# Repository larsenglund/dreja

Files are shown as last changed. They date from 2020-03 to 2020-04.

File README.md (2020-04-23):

# Dreja
DIY potter's wheel build from a broken hoverboard.

# Hardware
One of the wheel motors from the hoverboard/balance board is user as motor in the potter's wheel. The motor is controlled from a ESP32 via a brushless motor speed controller.

## Bill of materials
The hardware consists of
* Hoverboard, $0-? (I got mine for $30)
* Brushless Motor Speed Controller BLDC Driver Board with Hall (15A 500W DC12V-36V), $12
* ESP32 Development Board, $9
* Power supply (DC36V 10A 360W AC85-265V), $23
* Potentiometer for pedal (I used a 50k PTV09A-4025F-B503), $1
* Large bucket
* MDF + Scrap wood

Total cost: $60 (assuming you have the last two items on the list)

## Whishlist
Use the existing controlboard from the hoverboard to control the motor. There is a project that has done this for a different PCB than the one in my hoverboard, maybe it could easily be adapted.

## Assembly
First the motor is extracted from the hoverboard

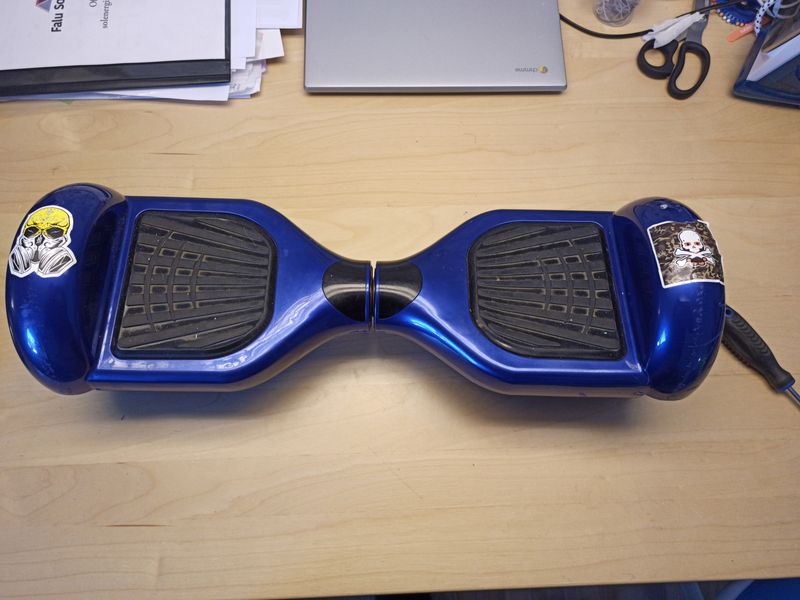
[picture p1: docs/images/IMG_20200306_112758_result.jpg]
Hoverboard1

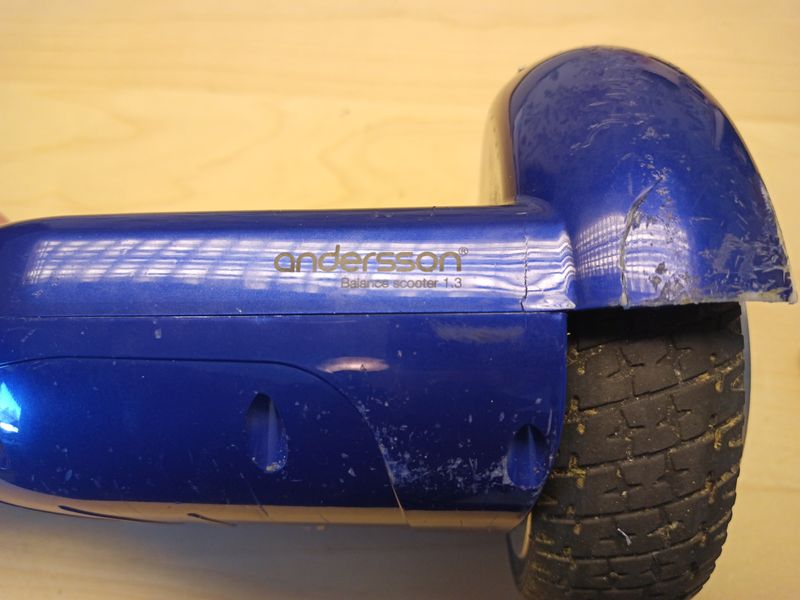
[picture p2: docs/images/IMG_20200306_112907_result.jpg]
Hoverboard2

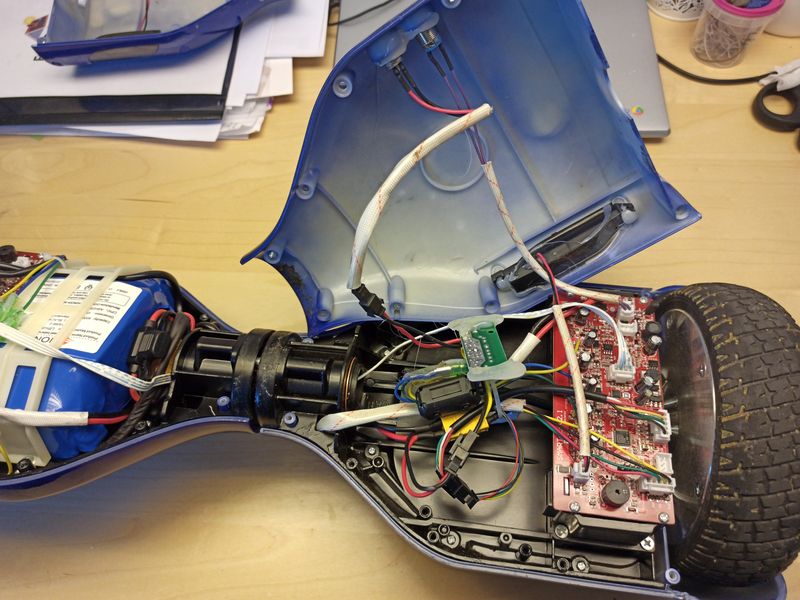
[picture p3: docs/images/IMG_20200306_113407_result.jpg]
Hoverboard3

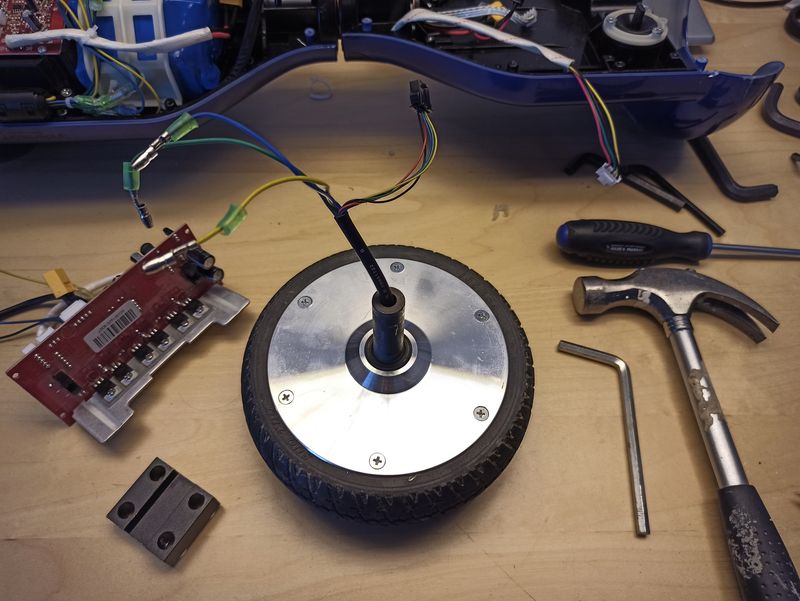
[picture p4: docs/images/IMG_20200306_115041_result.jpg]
Hoverboard4


### QS-909 JYQD
Low cost brushless motor driver with direction and speed control
12~36V, 500W (with heat sink) (http://grauonline.de/wordpress/?page_id=3122)

Pin description
* 5v       5v output
* EL       Motor enable input (5v)
* Signal   speedometer output
* Z/F      forward/reverse control (5v/GND)
* VR       speed control (0..5v)
* GND      ground

# Software
Software for the ESP32 is created with PlatformIO and allow speed control via a foot pedal. The ESP also serves up a captive portal that's used for remote monitoring and control.

Pin selection was made using this information.

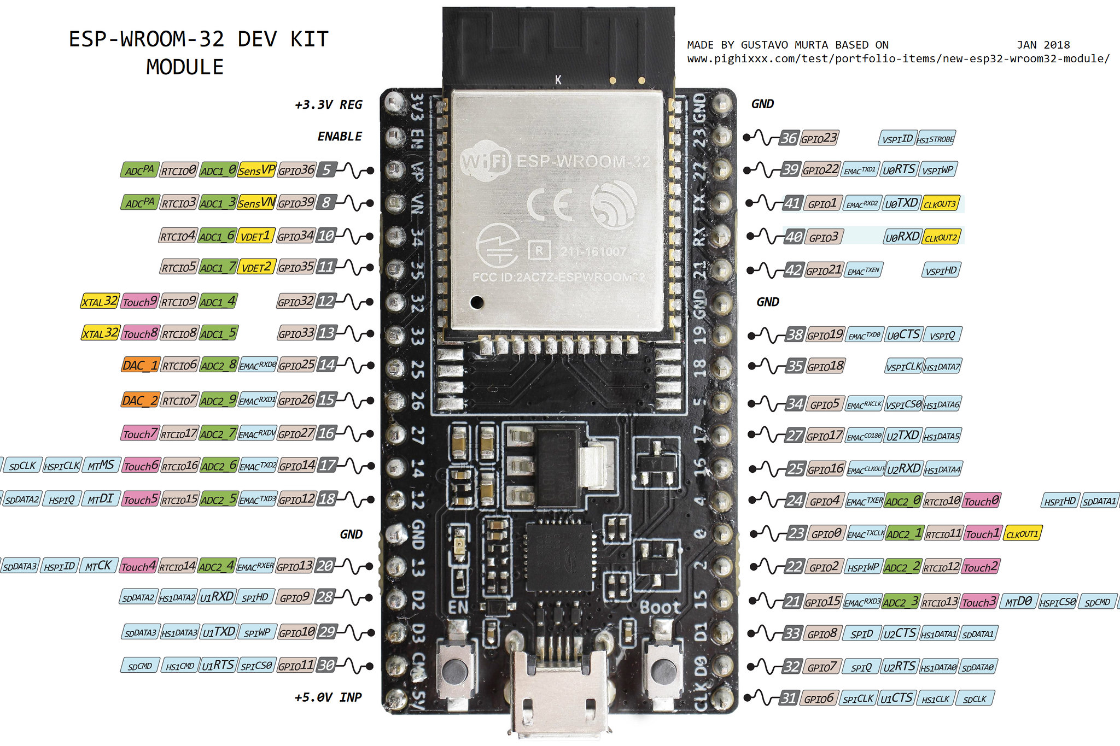
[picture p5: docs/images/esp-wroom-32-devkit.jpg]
ESP dev kit pins


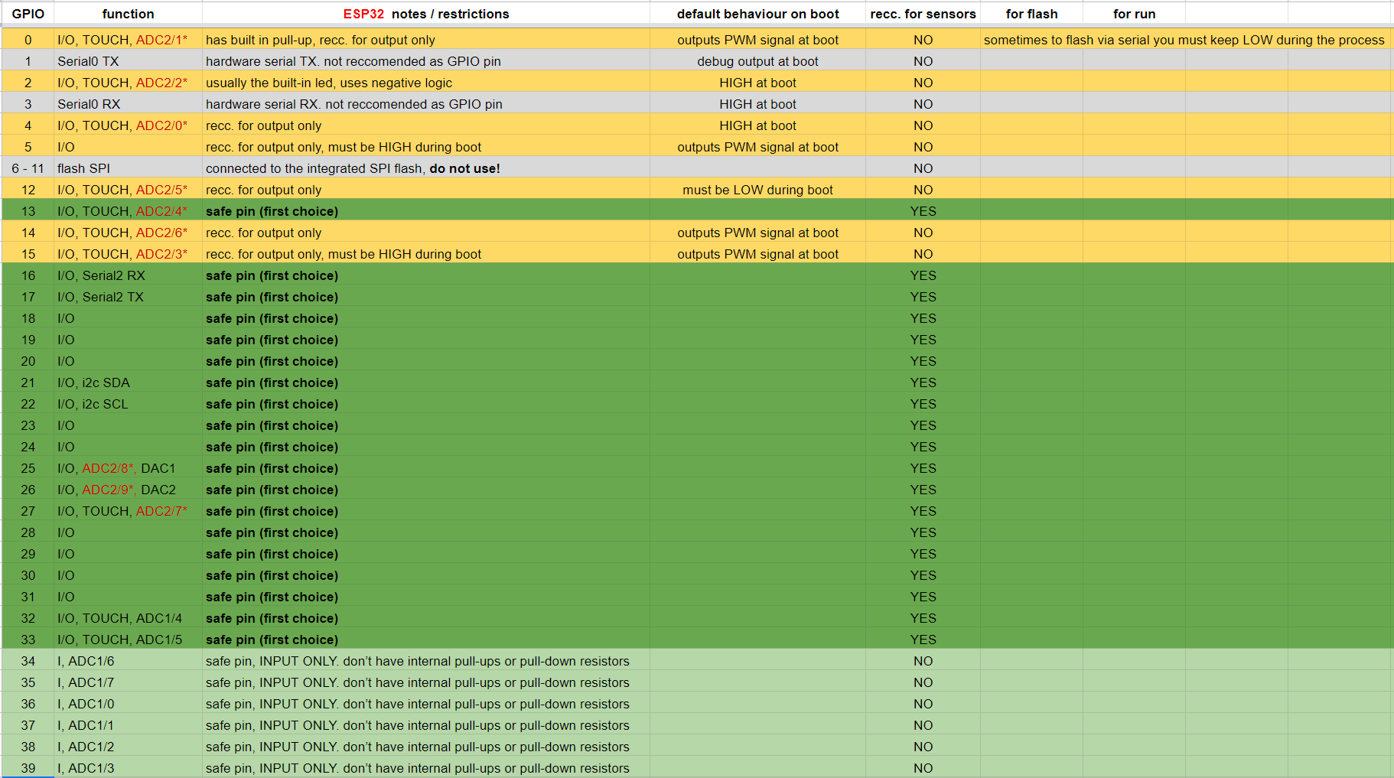
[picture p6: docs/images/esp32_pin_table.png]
ESP32 pins


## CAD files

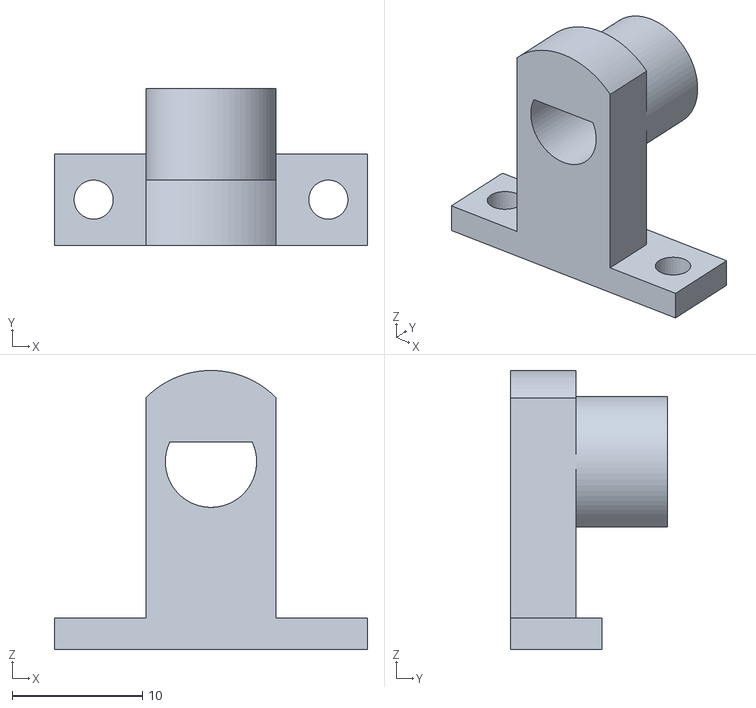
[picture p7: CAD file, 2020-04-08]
3D/Pedal1.stl
24.0 x 12.0 x 21.4

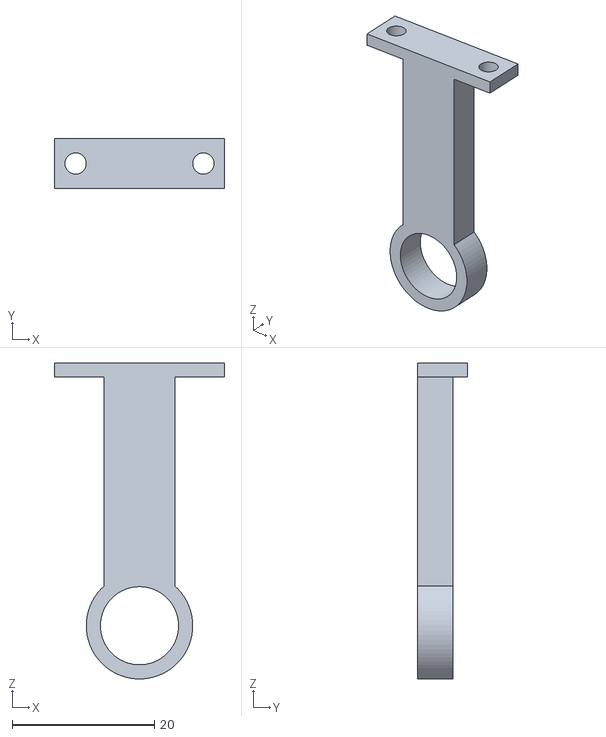
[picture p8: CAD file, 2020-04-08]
3D/Base.stl
24.0 x 7.00 x 44.5

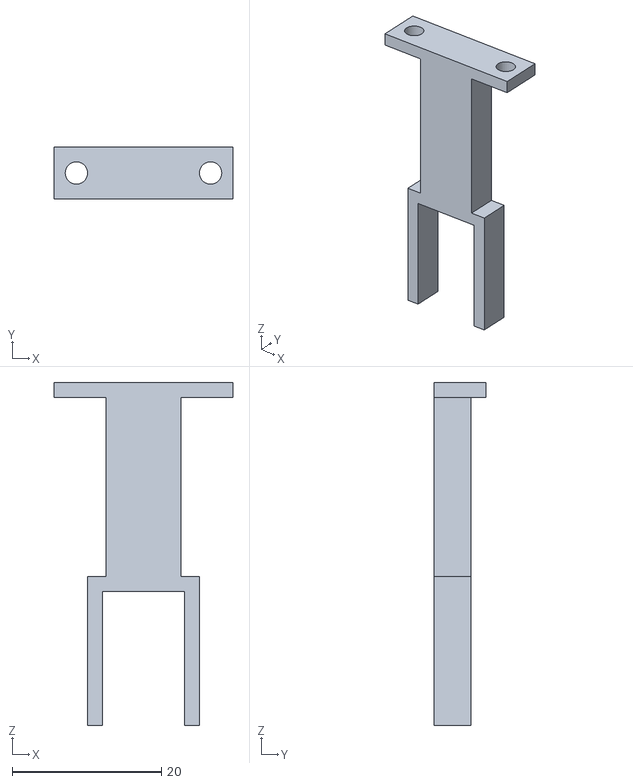
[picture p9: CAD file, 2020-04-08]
3D/PotHolder.stl
24.0 x 7.00 x 46.0

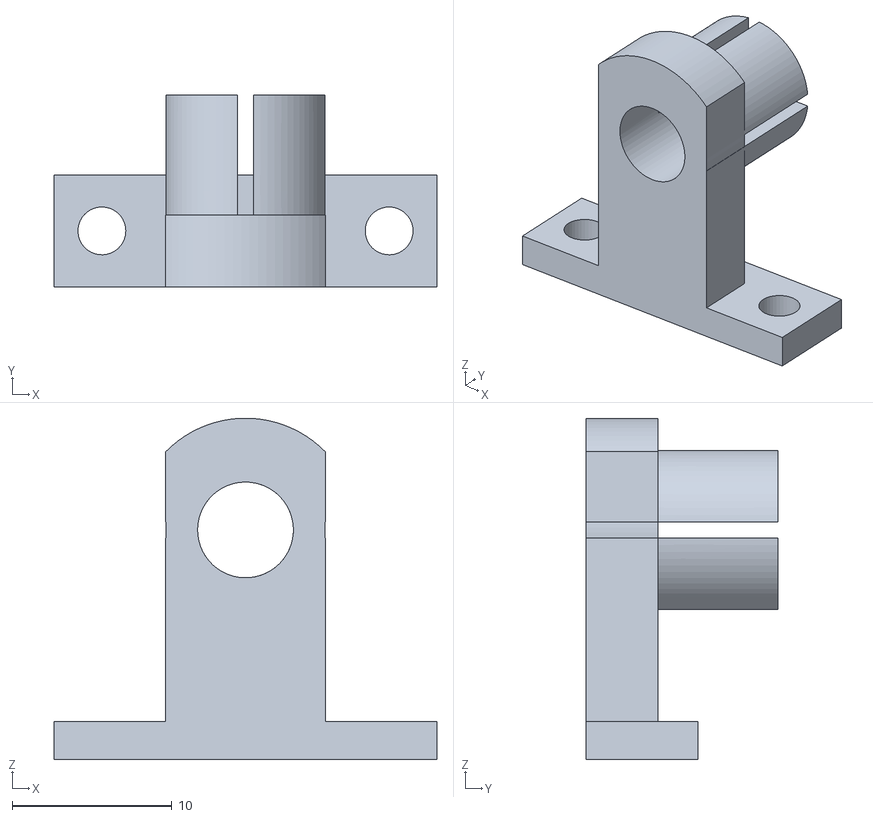
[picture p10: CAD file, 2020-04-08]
3D/Pedal2.stl
24.0 x 12.0 x 21.4

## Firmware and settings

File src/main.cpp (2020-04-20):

#include <Arduino.h>
#include <Adafruit_GFX.h>
#include <Adafruit_SSD1306.h>
#include <Fonts/Picopixel.h>
#include <Fonts/FreeSansBold9pt7b.h>

#define SCREEN_WIDTH 128 // OLED display width, in pixels
#define SCREEN_HEIGHT 64 // OLED display height, in pixels
// Declaration for SSD1306 display connected using software SPI (default case):
/*
#define OLED_MOSI  D7
#define OLED_CLK   D5
#define OLED_DC    D2
#define OLED_CS    D8
#define OLED_RESET D3
*/
#define OLED_MOSI  18
#define OLED_CLK   19
#define OLED_DC    16
#define OLED_CS    23
#define OLED_RESET 17
/*
orange-white: 5V (from motor controller)
orange:       GND (from motor controller)
green-white:  EL
green:        Signal
blue-white:   V/R
blue:         Z/F
brown-white:  3.3V (from ESP devboard)
brown:        TMP36 analog signal
*/
Adafruit_SSD1306 display(SCREEN_WIDTH, SCREEN_HEIGHT,
  OLED_MOSI, OLED_CLK, OLED_DC, OLED_RESET, OLED_CS);

/*
#define POT_PIN A0
#define PWM_PIN D4
#define RPM_PIN D1
*/
#define POT_PIN 36
#define PWM_PIN 26
#define RPM_PIN 27
#define DAC_PIN 25

int prev_x = 0;
int speed = 16; // pixels per second
int prev_timestamp = -1;
int dir = 1;
volatile bool update_text = true;
volatile float rpm = 0.0;
volatile int pot = 0;
volatile int prev_pot = 0;
volatile int rpm_count = 0;
int update_rpm_count = 0;
int rpm_timestamp = 0;


void updateText();
void drawAnimation();
int readPot();
ICACHE_RAM_ATTR void rpmISR();


void setup() {
  Serial.begin(115200);
  Serial.println(F("DREJA setup"));
  
  pinMode(LED_BUILTIN, OUTPUT);
  pinMode(POT_PIN, INPUT);
  pinMode(RPM_PIN, INPUT);//INPUT_PULLUP);
  attachInterrupt(digitalPinToInterrupt(RPM_PIN), rpmISR, FALLING);
  pinMode(PWM_PIN, OUTPUT);
  //analogWriteFreq(10000);
  ledcSetup(0, 10000, 12);
  ledcAttachPin(PWM_PIN, 0);

  // SSD1306_SWITCHCAPVCC = generate display voltage from 3.3V internally
  if(!display.begin(SSD1306_SWITCHCAPVCC)) {
    Serial.println(F("SSD1306 allocation failed"));
    for(;;); // Don't proceed, loop forever
  }
  //display.setRotation(1);
  display.setFont(&Picopixel);
  display.setTextColor(SSD1306_WHITE);
  display.setTextSize(1);
  display.clearDisplay();

  for (int n=0; n<4; n++) {
    digitalWrite(LED_BUILTIN, HIGH);
    delay(100);
    digitalWrite(LED_BUILTIN, LOW);
    delay(100);
  }
  Serial.println(F("Setup complete"));
}

void loop() {
  if (update_text) {
    update_text = false;
    display.clearDisplay();
    updateText();
  }

  pot = readPot();
  if (pot != prev_pot) {
    Serial.print("Pot: ");
    Serial.println(pot);
    //analogWrite(PWM_PIN, pot);
    ledcWrite(0, pot);
    update_text = true;
    prev_pot = pot;
  }

  if (++update_rpm_count >= 20) {
    float time = float(millis() - rpm_timestamp) / 1000.0;
    rpm = ((float)(60*rpm_count)) / 45.0 * 1.0/time; // find out actual numbers for hoverboard signal
    rpm_timestamp = millis();
    rpm_count = 0;
    update_rpm_count = 0;
    update_text = true;
  }

  drawAnimation();
  display.display();
  delay(50);
}

void updateText() {
  display.setFont(&Picopixel);
  display.setCursor(0,5);
  display.println(F("DREJA"));
  display.drawLine(0,7,128,7,SSD1306_WHITE);
  display.setCursor(0,14);

  display.println(F("RPM"));
  display.println();
  display.setFont(&FreeSansBold9pt7b);
  display.print(rpm, 0);  

  display.setFont(&Picopixel);
  display.println();
  display.println(F("POT"));
  display.println();
  display.setFont(&FreeSansBold9pt7b);
  display.print(pot);
  display.setFont(&Picopixel);
  display.println();
}

void drawAnimation() {
  int now = millis();
  if (prev_timestamp < 0) {
    prev_timestamp = millis();
  }
  int step = (now - prev_timestamp) * speed / 1000;
  int x = prev_x + step*dir;
  if (x >= display.width()) { // right bounce
    dir = -1;
    x = prev_x + step*dir;
  }
  else if (x < 0) { // left bounce
    dir = 1;
    x = prev_x + step*dir;
  }
  display.drawPixel(prev_x, display.height()-1, SSD1306_BLACK);
  display.drawPixel(x, display.height()-1, SSD1306_WHITE);
  prev_x = x;
  prev_timestamp = now;
  
}

int readPot() {
  int val = 0;
  for(int i = 0; i < 10; i++) {
    val += analogRead(A0);
    delay(5);
  }
  return val / 10;
}

void rpmISR() {
  rpm_count ++;
}

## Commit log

2020-04-08 Added 3D models for speed control pedal
    [Base.stl, Pedal1.stl, Pedal2.stl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]
2020-04-20 Switched to ESP32
